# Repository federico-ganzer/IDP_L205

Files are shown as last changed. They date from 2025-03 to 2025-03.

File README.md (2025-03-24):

#  It Doesn’t Perform - L205
This repository is for the Integrated Design Project (IDP) belonging to Team 205 done in Lent 2024-5. 

## Documentation:
- **Software:** ['docs.md'](docs.md)
- **Electrical:** ['IDP___Electrical_Documentation.pdf'](IDP___Electrical_Documentation.pdf) 
- **Mechanical:** [Mechanical Documentation.pdf](https://github.com/federico-ganzer/IDP_L205/blob/main/Mechanical%20Documentation.pdf)

## Our Team:
- Somanshu - Software
- Josh - Electrical/Software
- Alex - Electrical/Mechanical
- Hayyan - Mechanical
- Tom - Mechanical
- Djaafar - Mechanical
- Federico - Software

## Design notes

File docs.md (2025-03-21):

# Team L205 IDP Software Documentation

  


## Table of Contents

1. [Structure and Algorithms](#Structureandapplication)
2. [Modules](#modules)

## Structure and Algorithms
The general approach of the software structure was to create an AGV class (`Robot()`) that could be used to access motor control, sensor readings, and storing of current state variables associated to what the robot's current task is. The AGV class would respond to changes in its current route and move from node to node accordingly. The `current_node` state variable is updated to the next node in the current route whenever a junction is detected. At each detected junction a decision function is called to determine whether the robot should turn, and the `current_direction` variable is adjusted accordingly.
<div align="center">
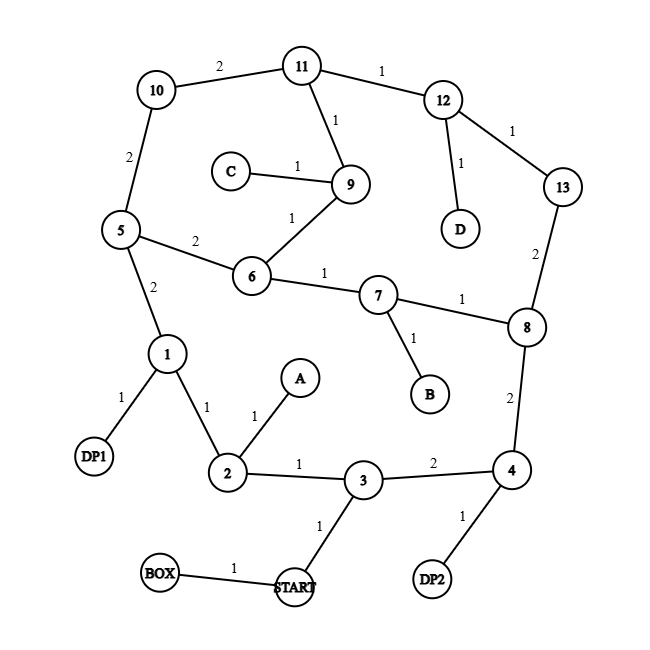
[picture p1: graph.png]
Graph
  
  <p><em>Figure 1: Graph of town with `node_id` and edge values used by `pathfinder.py`</em></p>
</div>

For our use, the `Robot()` pins are set as follows (these can be changed in the pins dict passed to `Robot()` when initializing):
```
pins = {'outer_sensorL_pin' : 18, 'outer_sensorR_pin' : 19,
        'line_sensorR_pin' : 20, 'line_sensorL_pin' : 21,
        'motorR_pwm_pin' : 4, 'motorR_dir_pin' : 5, # Motor Pins are Hard Coded in Robot()
        'motorL_pwm_pin' : 6, 'motorL_dir_pin' : 7, # Motor Pins are Hard Coded in Robot()
        'servo_pin1' : 13, 'servo_pin2' : 15,
        'led_pin' : 22, 'button_pin': 12 }
```
Each number represents the corresponding GPIO pin on the picobot.

The main loop (in `main.py`) starts by initialising the robot with the current target of `A`. Once the robot navigates to its target, it enters the pickup routine and initializes a new route based on the colour of the package it picked up. The route is then navigated, the block is dropped and a new route is initialized to the closest non-visited customer. The process is repeated until all customers have been visited. The robot then returns to the start box.

```mermaid
flowchart TD
    Start([Start]) --> Initialize[Initialize Robot with pins and targets]
    Initialize --> SetServo[Set servo to zero]
    SetServo --> |Move Forward| MoveForward[Move forward at speed 100 along current_route]

    MoveForward --> |Check Current Node| CheckNode{Is current node in customers?}
    CheckNode --> |Yes| Pickup[Perform pickup operation]
    CheckNode --> |No| CheckDepot{Is current node in depots?}

    Pickup --> |Continue| MoveForward

    CheckDepot --> |Yes| Drop[Perform drop operation]
    CheckDepot --> |No| MoveForward

    Drop --> |Find Closest Customer| FindClosest[Find closest unvisited customer]
    FindClosest --> |Update Target and Route| UpdateTarget[Set current_target and current_route]
    UpdateTarget --> |Continue| MoveForward

    Drop --> |Check if All Customers Visited| CheckAllVisited{Are all customers visited?}
    CheckAllVisited --> |Yes| ReturnToStart[Set target to START and plan route]
    CheckAllVisited --> |NO| FindClosest
    ReturnToStart --> |Continue| MoveForward

    MoveForward --> |Check if at START| CheckStart{Is current node START and target START?}
    CheckStart --> |Yes| Stop[Stop motors and end program]
    CheckStart --> |No| MoveForward

    Stop --> End([End])
```
<div align="center">
<p><em>Figure 2: Diagram of main loop</em></p>
</div>

## Modules
- [robot.py](#robot.py)
- [pathfinder.py](#pathfinder.py)
- [Sensors](#sensors)
- [motors.py](#motors.py)

### `robot.py`

**Description:** Contains `Robot(i2c_bus, pins[dict], start, target1)` class. `Robot()` contains methods for AGV control for manouvring and collecting/depositing loads. Class is initialised with i2c pins and pin numbers associated with the servos, motors and sensors and can be easily modified as a modular system (eg. if sensor or servo additions are made). `start` and `target1` (in `node_id` form) are necessary to set the first route the `Robot()` should follow.

**Methods:**
-  `forward()`: Drives robot motors at desired speed with line following and junction decision logic. Uses PID control for straight line following from [`follow_line()`](#follow_line).

-  `turn()`: Following a call to [`junction_decision()`](#junction_decision), the robot performs a 90 degree turn in the direction set by `junction_decision()`, provided that junction type also satisfies the turn. The current state variables are then updated. This checks that the middle sensor (on the side opposite to that of the direction of tha turn) is on the line and then exits the function, such that the PID control in `forward()` is reinitiated. Boolean `with_prep = True` determines if a turning prep-time should be added. During this prep-time the robot continues forward for a set time interval before turning. `with_prep` should be turned false if turning from a reverse position.

-  `junction_decision()`: Using a 2D vector product between the current and next direction, the function returns a value that when positive indicates a left turn, when negative, a right turn, and when zero straight. If the `Robot()` is at the end of the `current_route`, the robot stops.

-  `detect_junction()`: Uses the two outer line sensors to detect junctions. If a junction is detected [`junction_decision()`](#junction_decision) is called and the position of `current_node`(graphical representation of position) is updated in [`forward()`](#forward).

-  `follow_line()`: Implements PID control with two line sensor inputs straddling the line to follow the line. PID weights can be adjusted in `self.kp`, `self.ki`, and `self.kd`.

-  `spin()`: Performs a spin by 180 degrees. This will check that the configuration of the robot has now been realligned also (to an approximate degree) before the `follow_line()` takes over again.

-  `pickup()`: Routine actuates the servo to pick up the block. The colour of the block is identified and the according depot is assigned as the `self.current_target`, creating a new route for `Robot()` to follow in forward. The `Robot()` will turn out of the customer zone accordingly.

-  `drop()`: Actuates the servo to drop the block. Then the next closest customer is determined for `Robot()`. The `Robot()` turns out of the depot, facing away from the wall to avoid collision, and then exits the routine. 

### `pathfinder.py`

**Description:** Makes use of adjacency table of graph and Dijkstra's algorithm to find the minimal distance path from a given `start` node to `end` node. Includes a map from each node to their coordinate in physical space, which is used to determine which direction turns need to be made in.

**Functions:**
- `dijkstra(adj_list, start, end)`: Applies dijkstra's algorithm between `start` and `end` nodes (in `node_id` form) when prodived with `adj_list` of the underlying graph (map) and returns a tuple containing the list of the coordinates of nodes in a route (not including `start`) and the total length of the route.

- `convert_coord_to_node(coord)`: Uses the `coord_to_node` dictionary to convert phyical coordinates of nodes to their respective `node_id`.

### `motors.py`
**Description:** Includes two class definitions that are used primarily in the `robot.py`, that controls the motor movements as well as servo movements. 

#### `Motor(dir_pin, pwm_pin)`
Takes parameters of the pins used, and has the following methods:
- `self.forward(speed)`
- `self.reverse(speed)`
- `self.stop()`

#### `Servo(pwn_pin)`
Takes parameters of the pin (singular) used. It has the following methods:
- `set_angle(angle)`
- `zero()`

### Sensors
**File:** `tcs34725.py`
**Description:**  Includes the class TCS34725, which contains methods for initialising the colour sensor as well as reading the colour temperature, which is used in [`pickup()`](#pickup) to identify the colour of the block that has been picked up. 

**File:** `vl53l0x.py`
**Description:** Includes the class for the ToF sensor, which is not used but could be implemented in the `Robot()` class.

## License

```
MIT License

Copyright (c) 2024 

Permission is hereby granted, free of charge, to any person obtaining a copy
of this software and associated documentation files (the "Software"), to deal
in the Software without restriction, including without limitation the rights
to use, copy, modify, merge, publish, distribute, sublicense, and/or sell
copies of the Software, and to permit persons to whom the Software is
furnished to do so, subject to the following conditions:

The above copyright notice and this permission notice shall be included in all
copies or substantial portions of the Software.

THE SOFTWARE IS PROVIDED "AS IS", WITHOUT WARRANTY OF ANY KIND, EXPRESS OR
IMPLIED, INCLUDING BUT NOT LIMITED TO THE WARRANTIES OF MERCHANTABILITY,
FITNESS FOR A PARTICULAR PURPOSE AND NONINFRINGEMENT. IN NO EVENT SHALL THE
AUTHORS OR COPYRIGHT HOLDERS BE LIABLE FOR ANY CLAIM, DAMAGES OR OTHER
LIABILITY, WHETHER IN AN ACTION OF CONTRACT, TORT OR OTHERWISE, ARISING FROM,
OUT OF OR IN CONNECTION WITH THE SOFTWARE OR THE USE OR OTHER DEALINGS IN THE
SOFTWARE.
```

---

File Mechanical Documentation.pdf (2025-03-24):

Mechanical Documentation

Assembly Drawing
Laser Cut MDF Part Drawings Sheet Metal Drawings
DFX Files Used for Laser Cutting

Material Choice

The two main materials in manufacturing were MDF and 1.4mm Aluminum plate. MDF was chosen over Plywood due to it being slightly stronger and less flexible, without really affecting the weight. Aluminum was chosen over Steel, as it was thicker for a similar weight and hence resulted in less bending and warping. We chose not to do any 3D printing as this is time consuming and didn't allow for rapid prototyping and modification.

Assembly

We preferred to use bolts when assembling as this allowed for easy deconstruction and modification. Wood glue was used to fit together the finger joint boxes for the Picobot and the Battery. We also sometimes had to make use of washers and bolts to offset pieces to the required position. Holes for bolts are marked on the sheet metal pieces in the drawing, although there are no holes marked on the drawings for wooden pieces as we found it easy to simply mark these holes with a pencil using the holes from the other pieces that were to be fitted, this allowed for the best positioning and alignment.

E

E

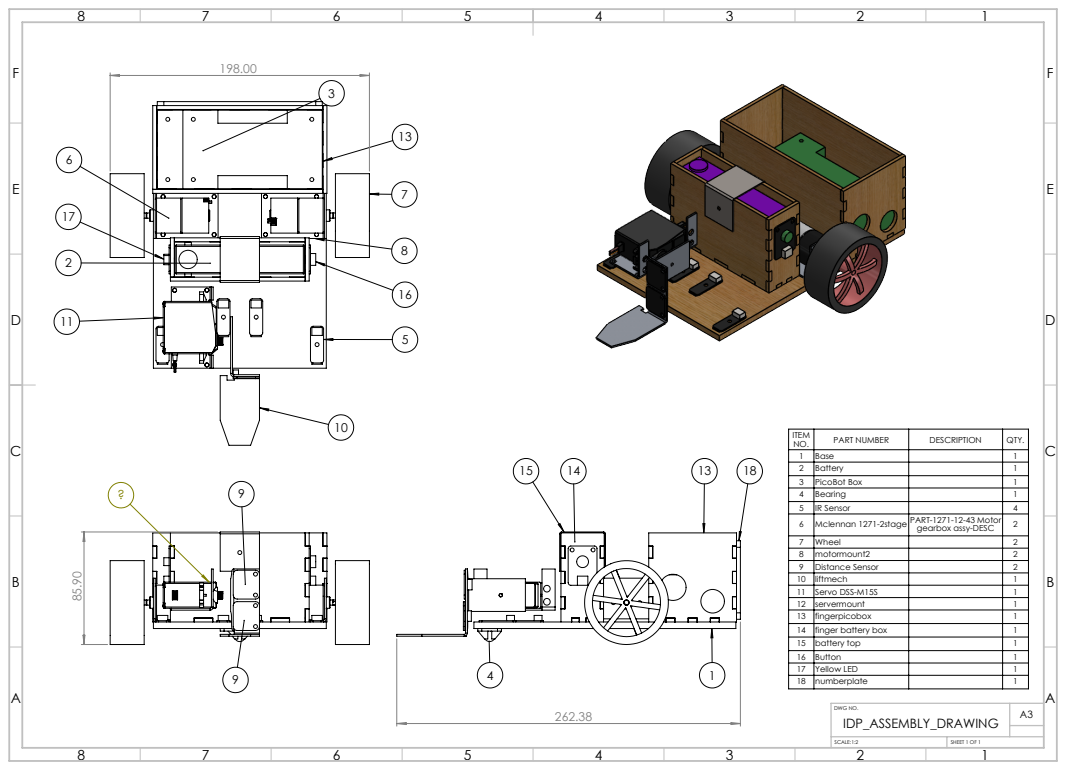
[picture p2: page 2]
ITEM; PART NUMBER; DESCRIPTION; QTY. 1; Base; Battery; PicoBot Box; Bearing; IR Sensor; Mclennan 1271-2stage PART-1271-12-43 Motor; SHEET 1 OF 1; IDP_ASSEMBLY_DRAWING; SCALE:1:2; DWG NO.

gearbox assy-DESC | 2

7 | Wheel | | 2
8 | motormount2 | | 2
9 | Distance Sensor | | 2
10 | liftmech | | 1
11 | Servo DSS-M15S | | 1
12 | servermount | | 1
13 | fingerpicobox | | 1
14 | finger battery box | | 1
15 | battery top | | 1
16 | Button | | 1
17 | Yellow LED | | 1
18 | numberplate | | 1

G | G
H | H

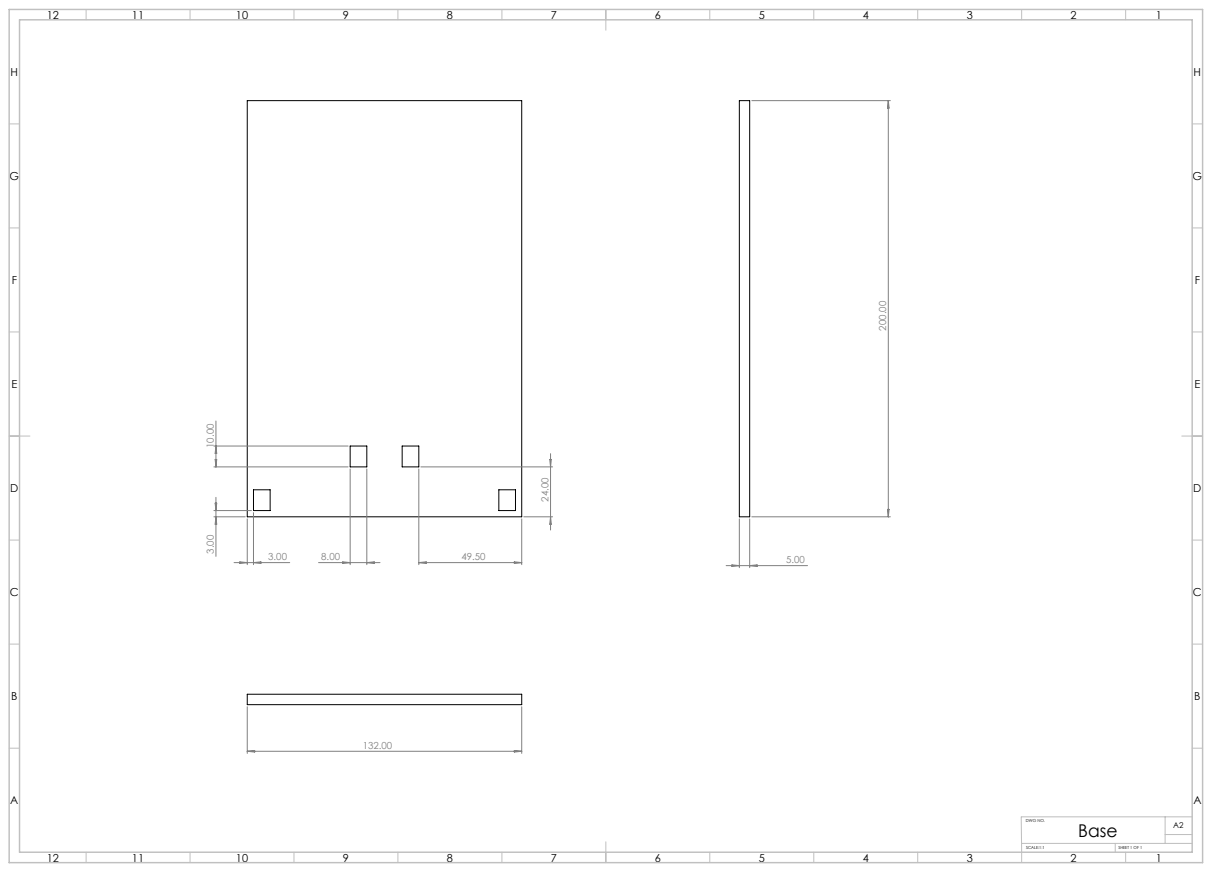
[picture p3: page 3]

Base

SCALE:1:1 | SHEET 1 OF 1

G | G
H | H

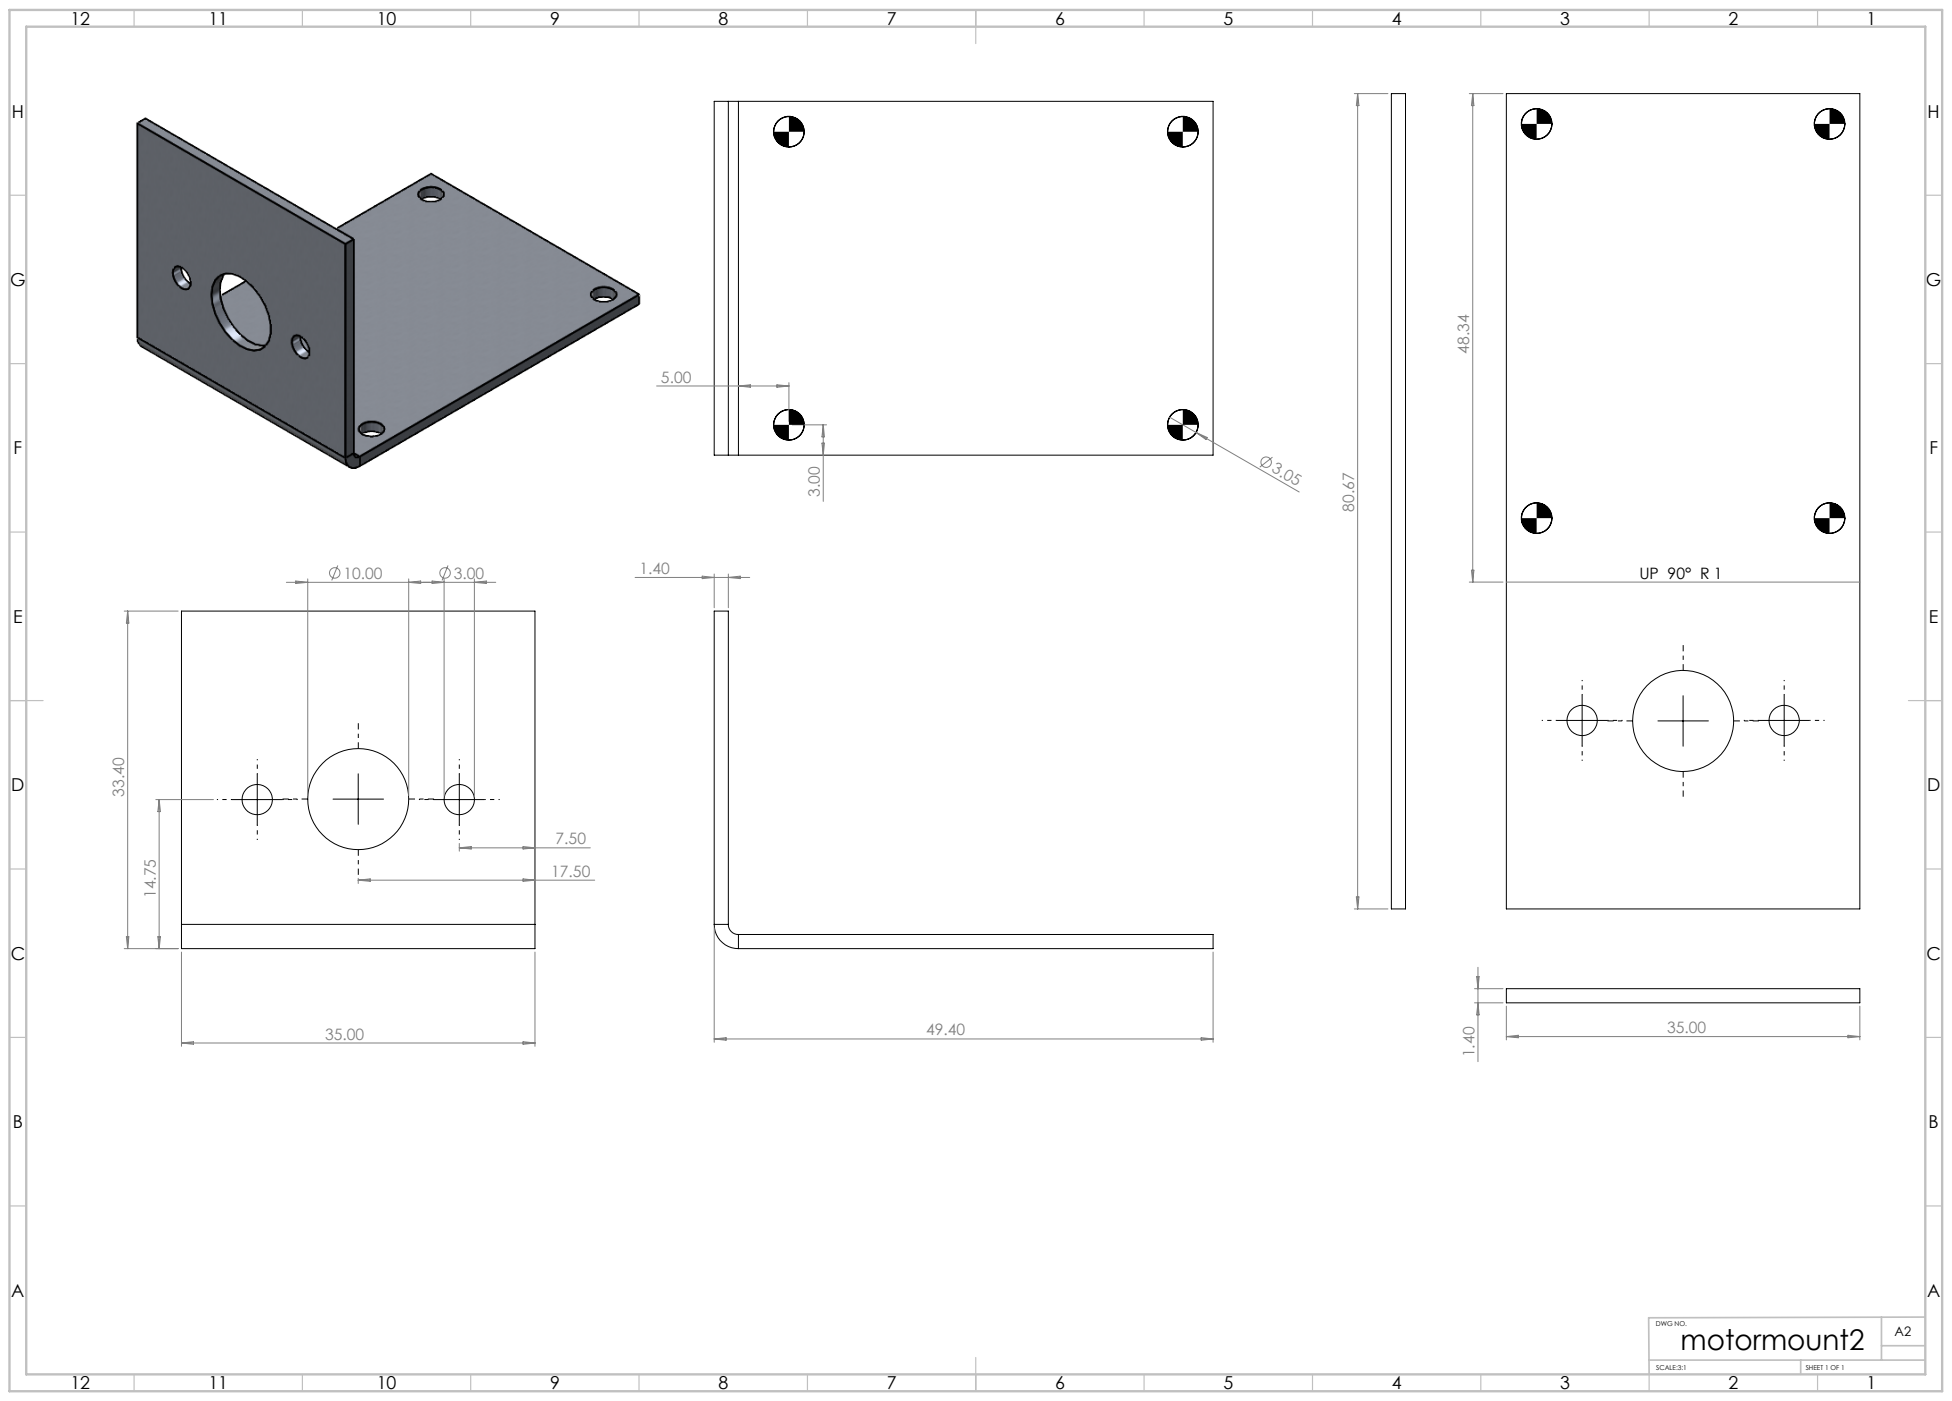
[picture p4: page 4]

motormount2

SCALE:3:1 | SHEET 1 OF 1

G

G

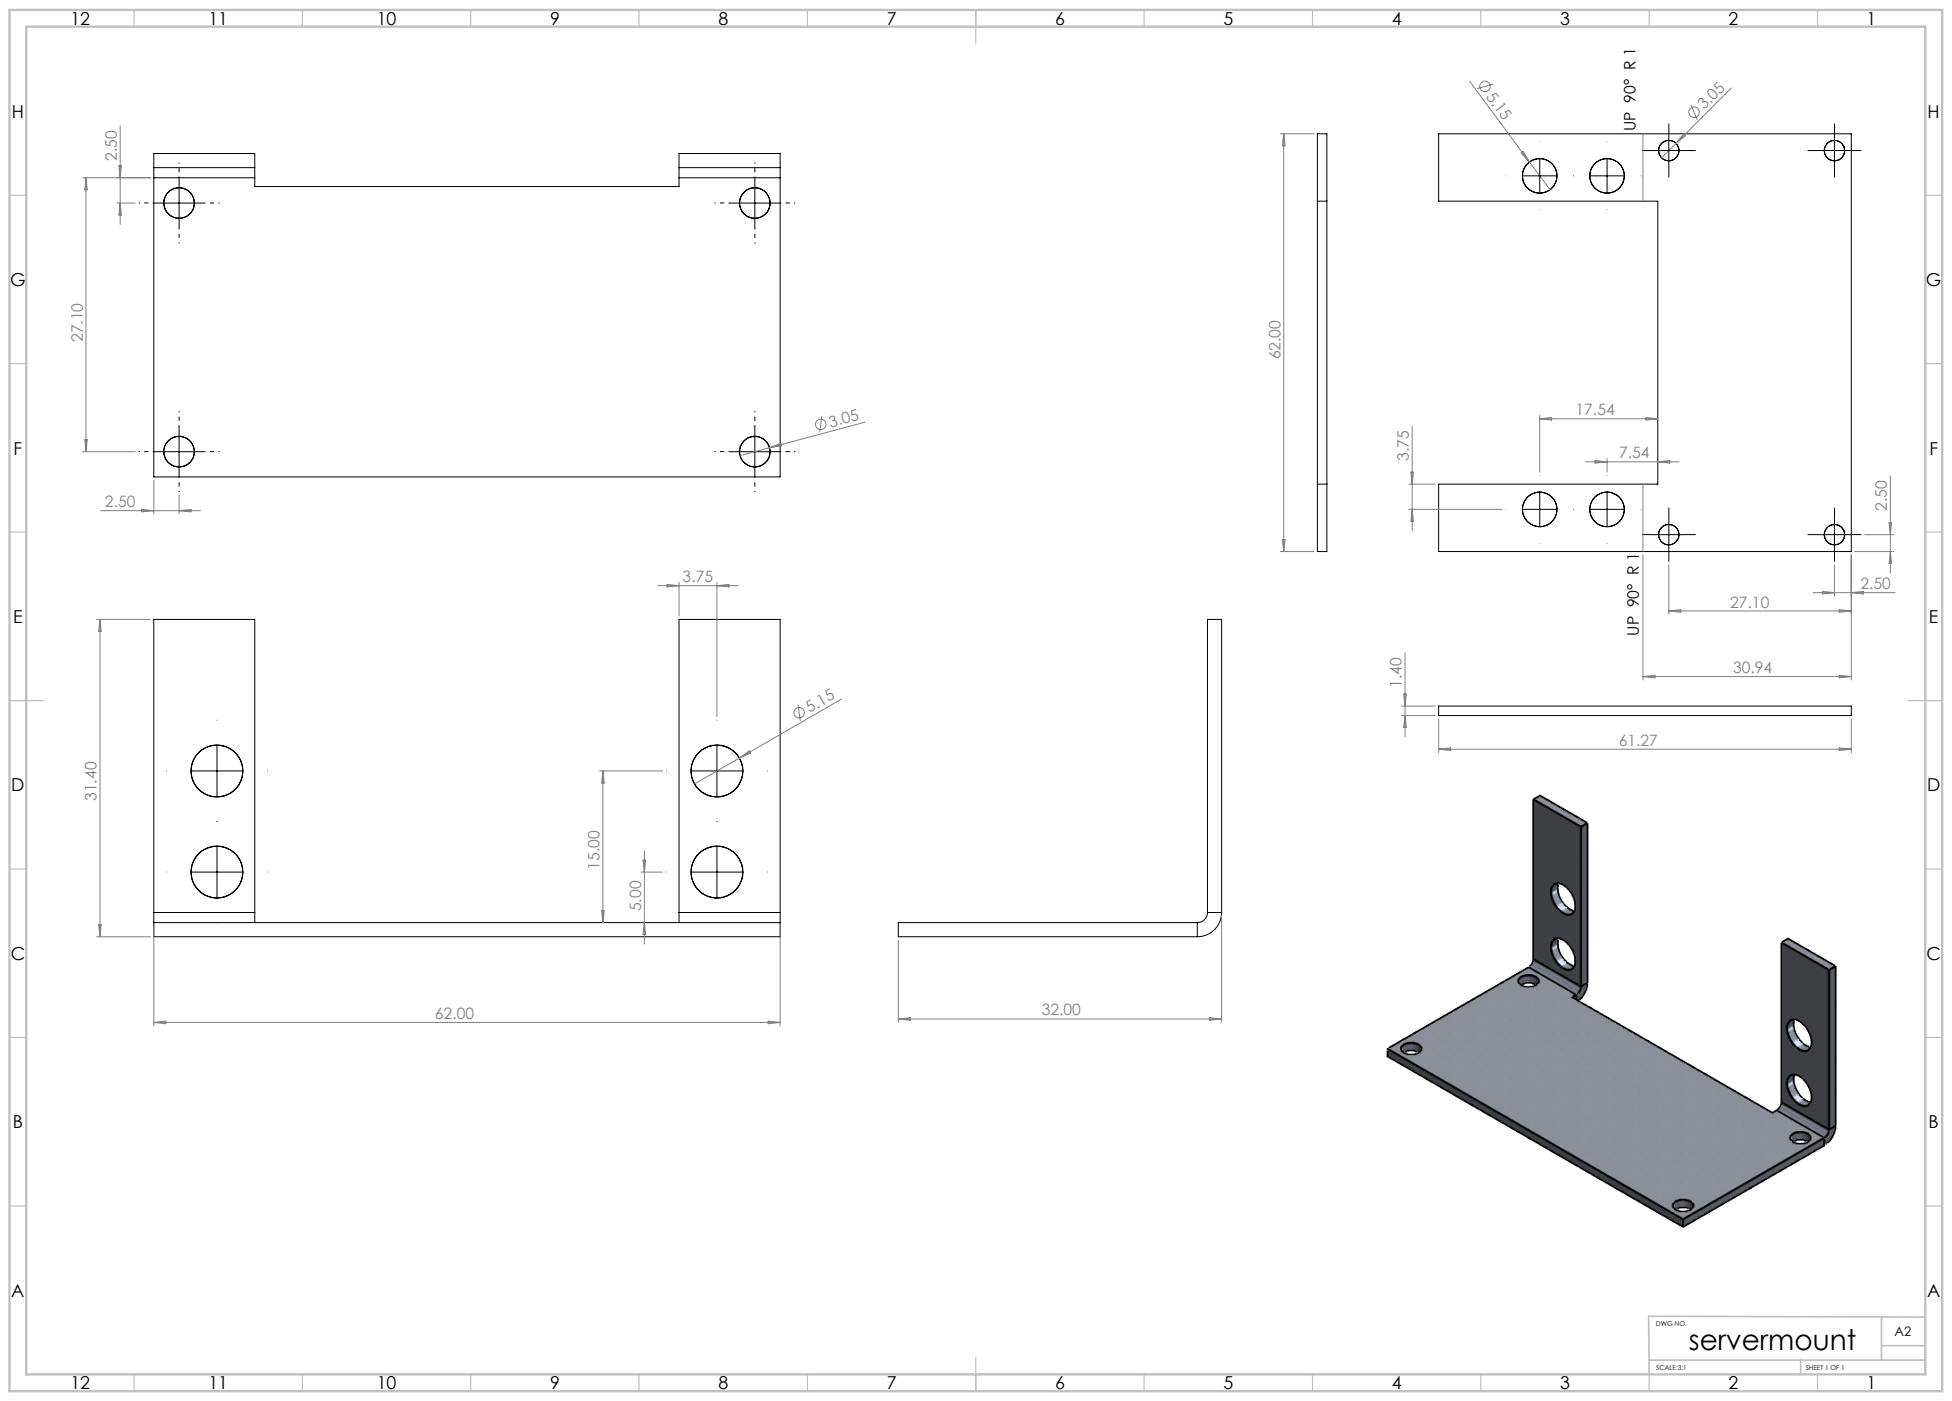
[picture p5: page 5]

servermount

SCALE:3:1 | SHEET 1 OF 1

G

G

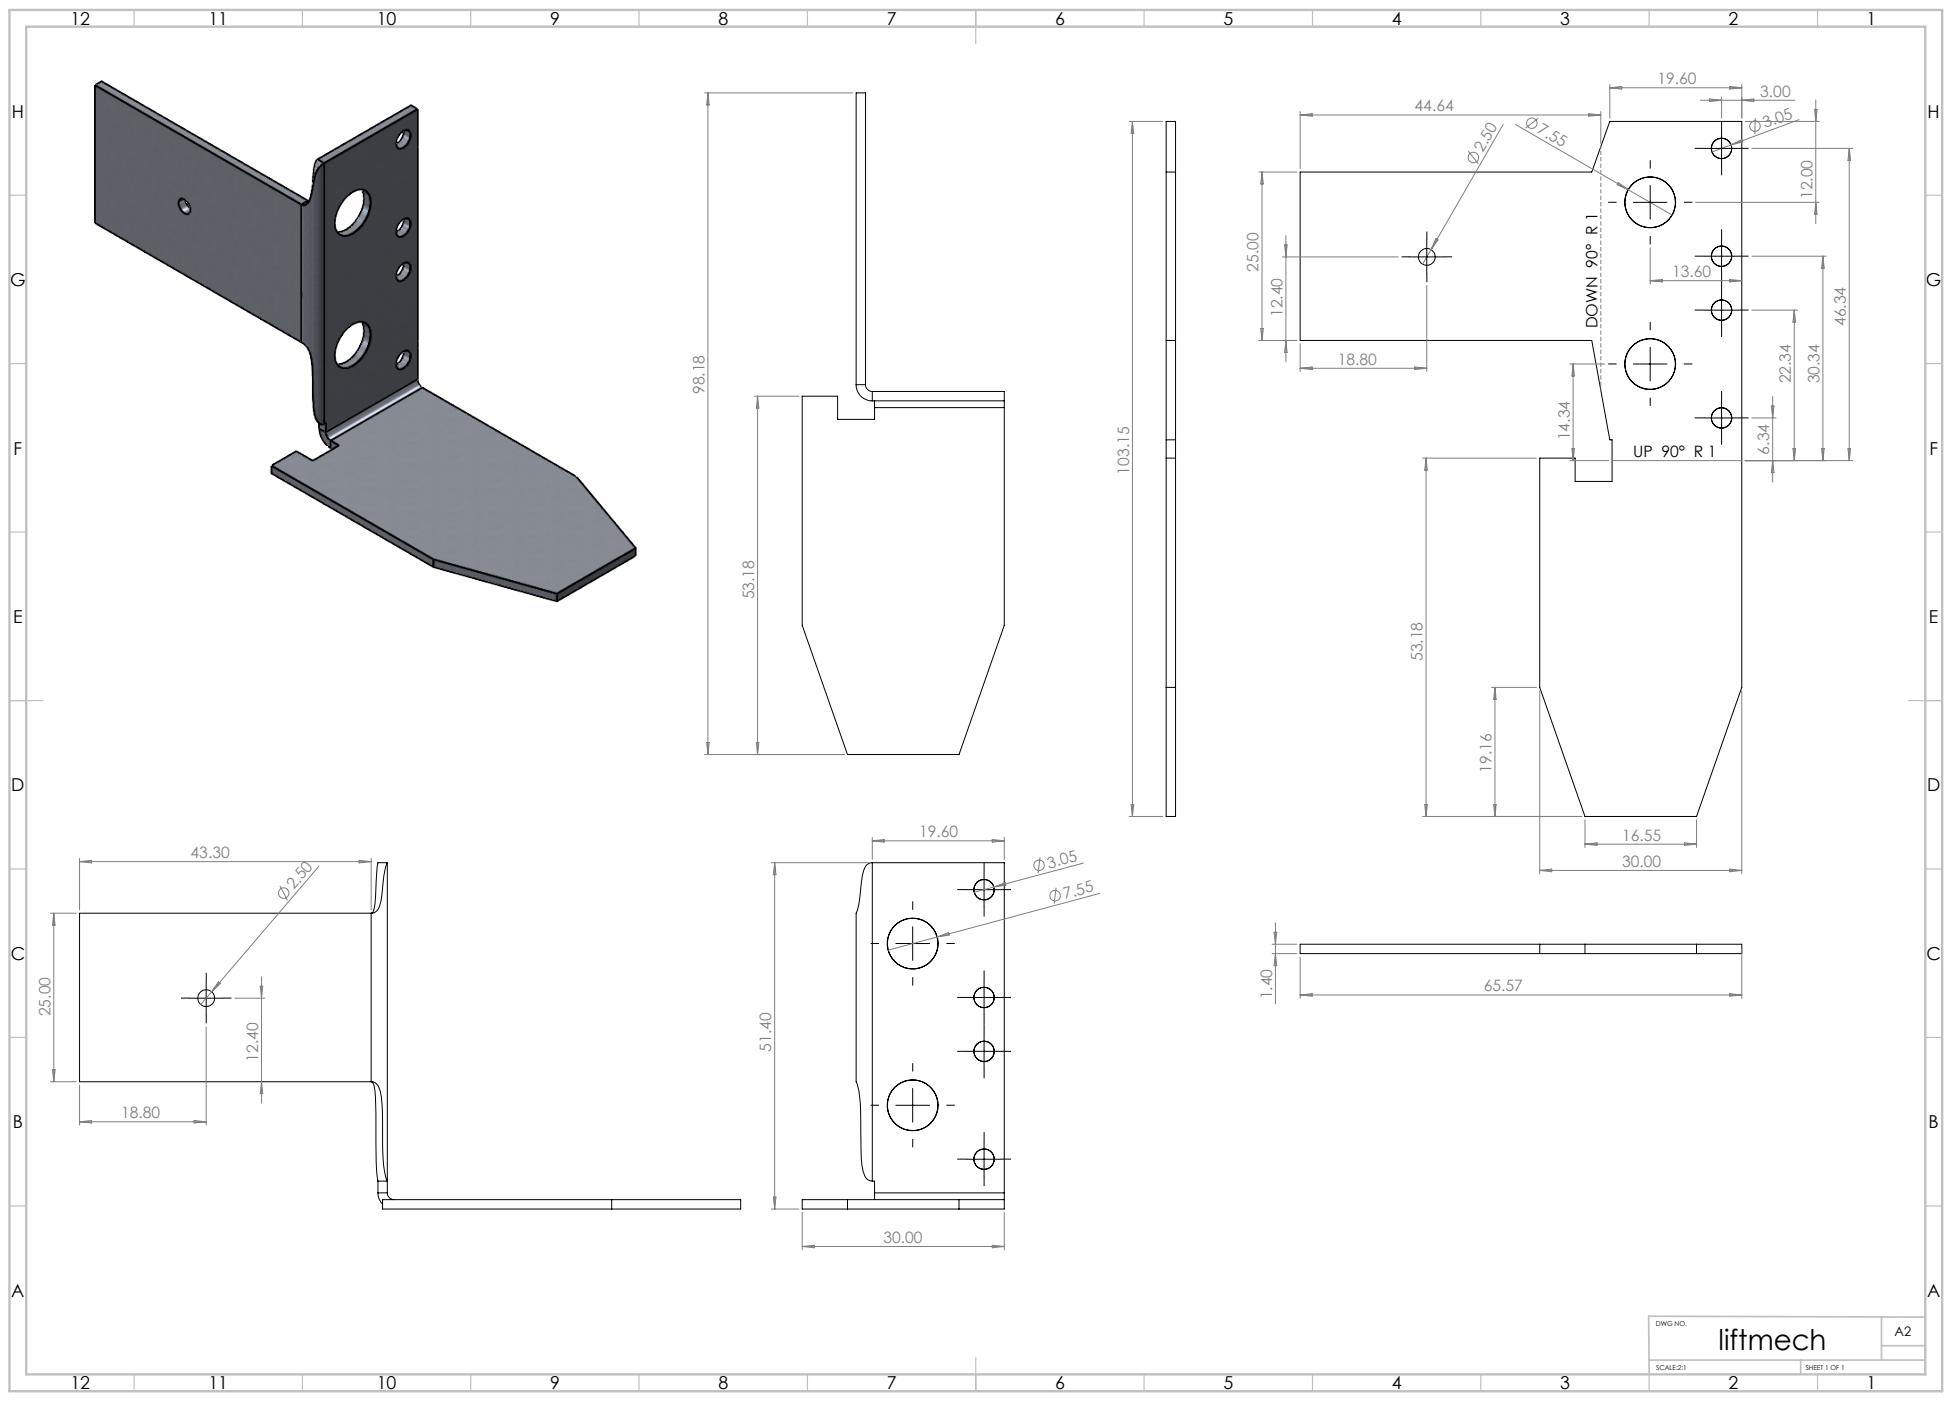
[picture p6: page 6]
DOWN 90° R 1

liftmech

SCALE:2:1 | SHEET 1 OF 1

G | G
H | H

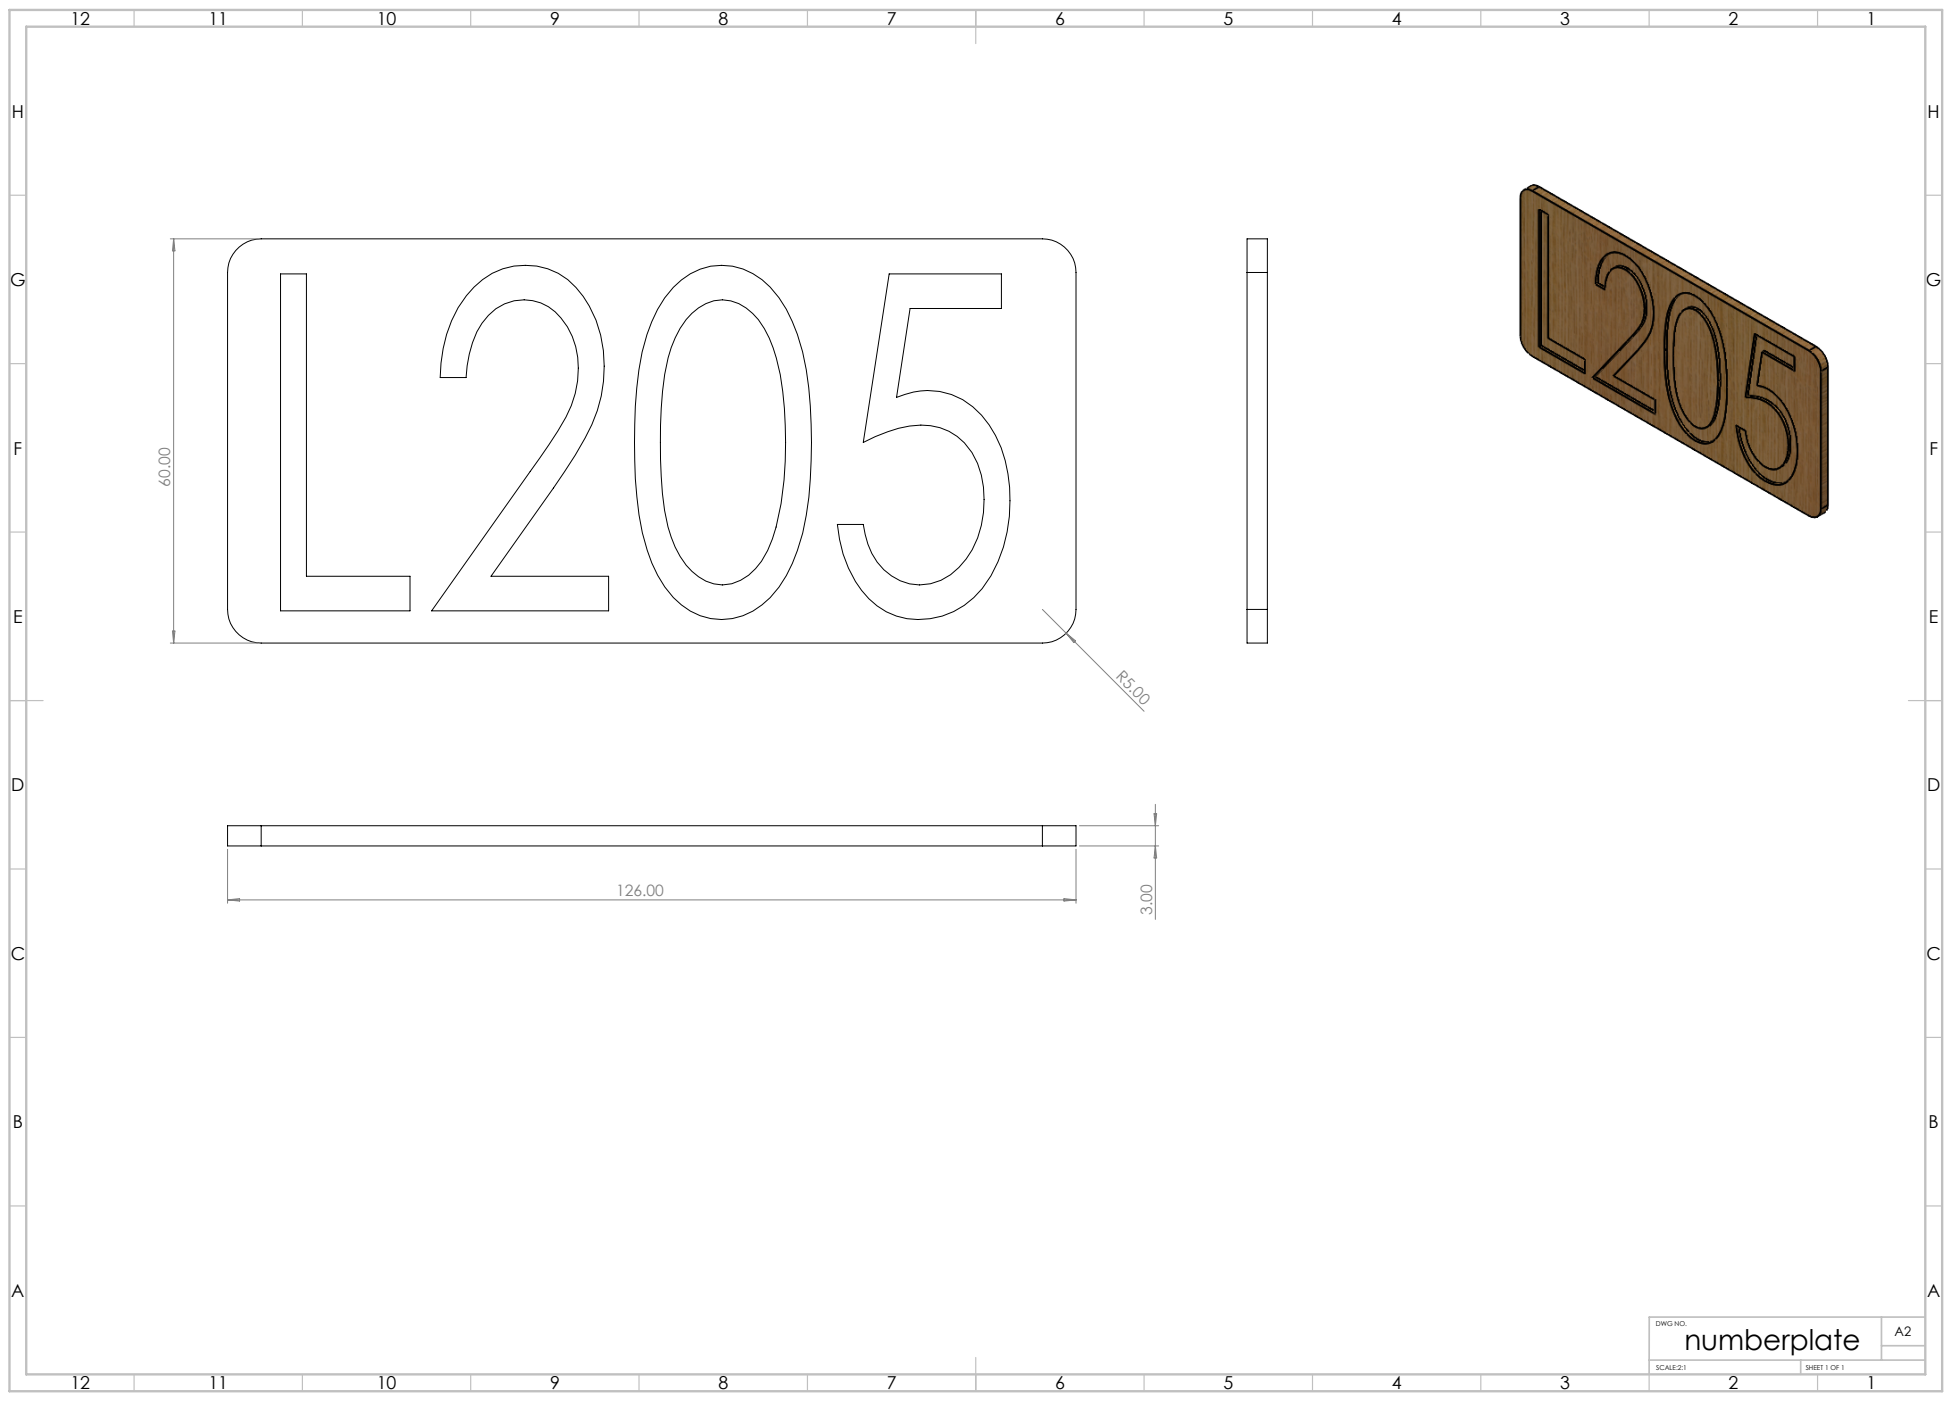
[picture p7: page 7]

numberplate

SCALE:2:1 | SHEET 1 OF 1

G | G
H | H

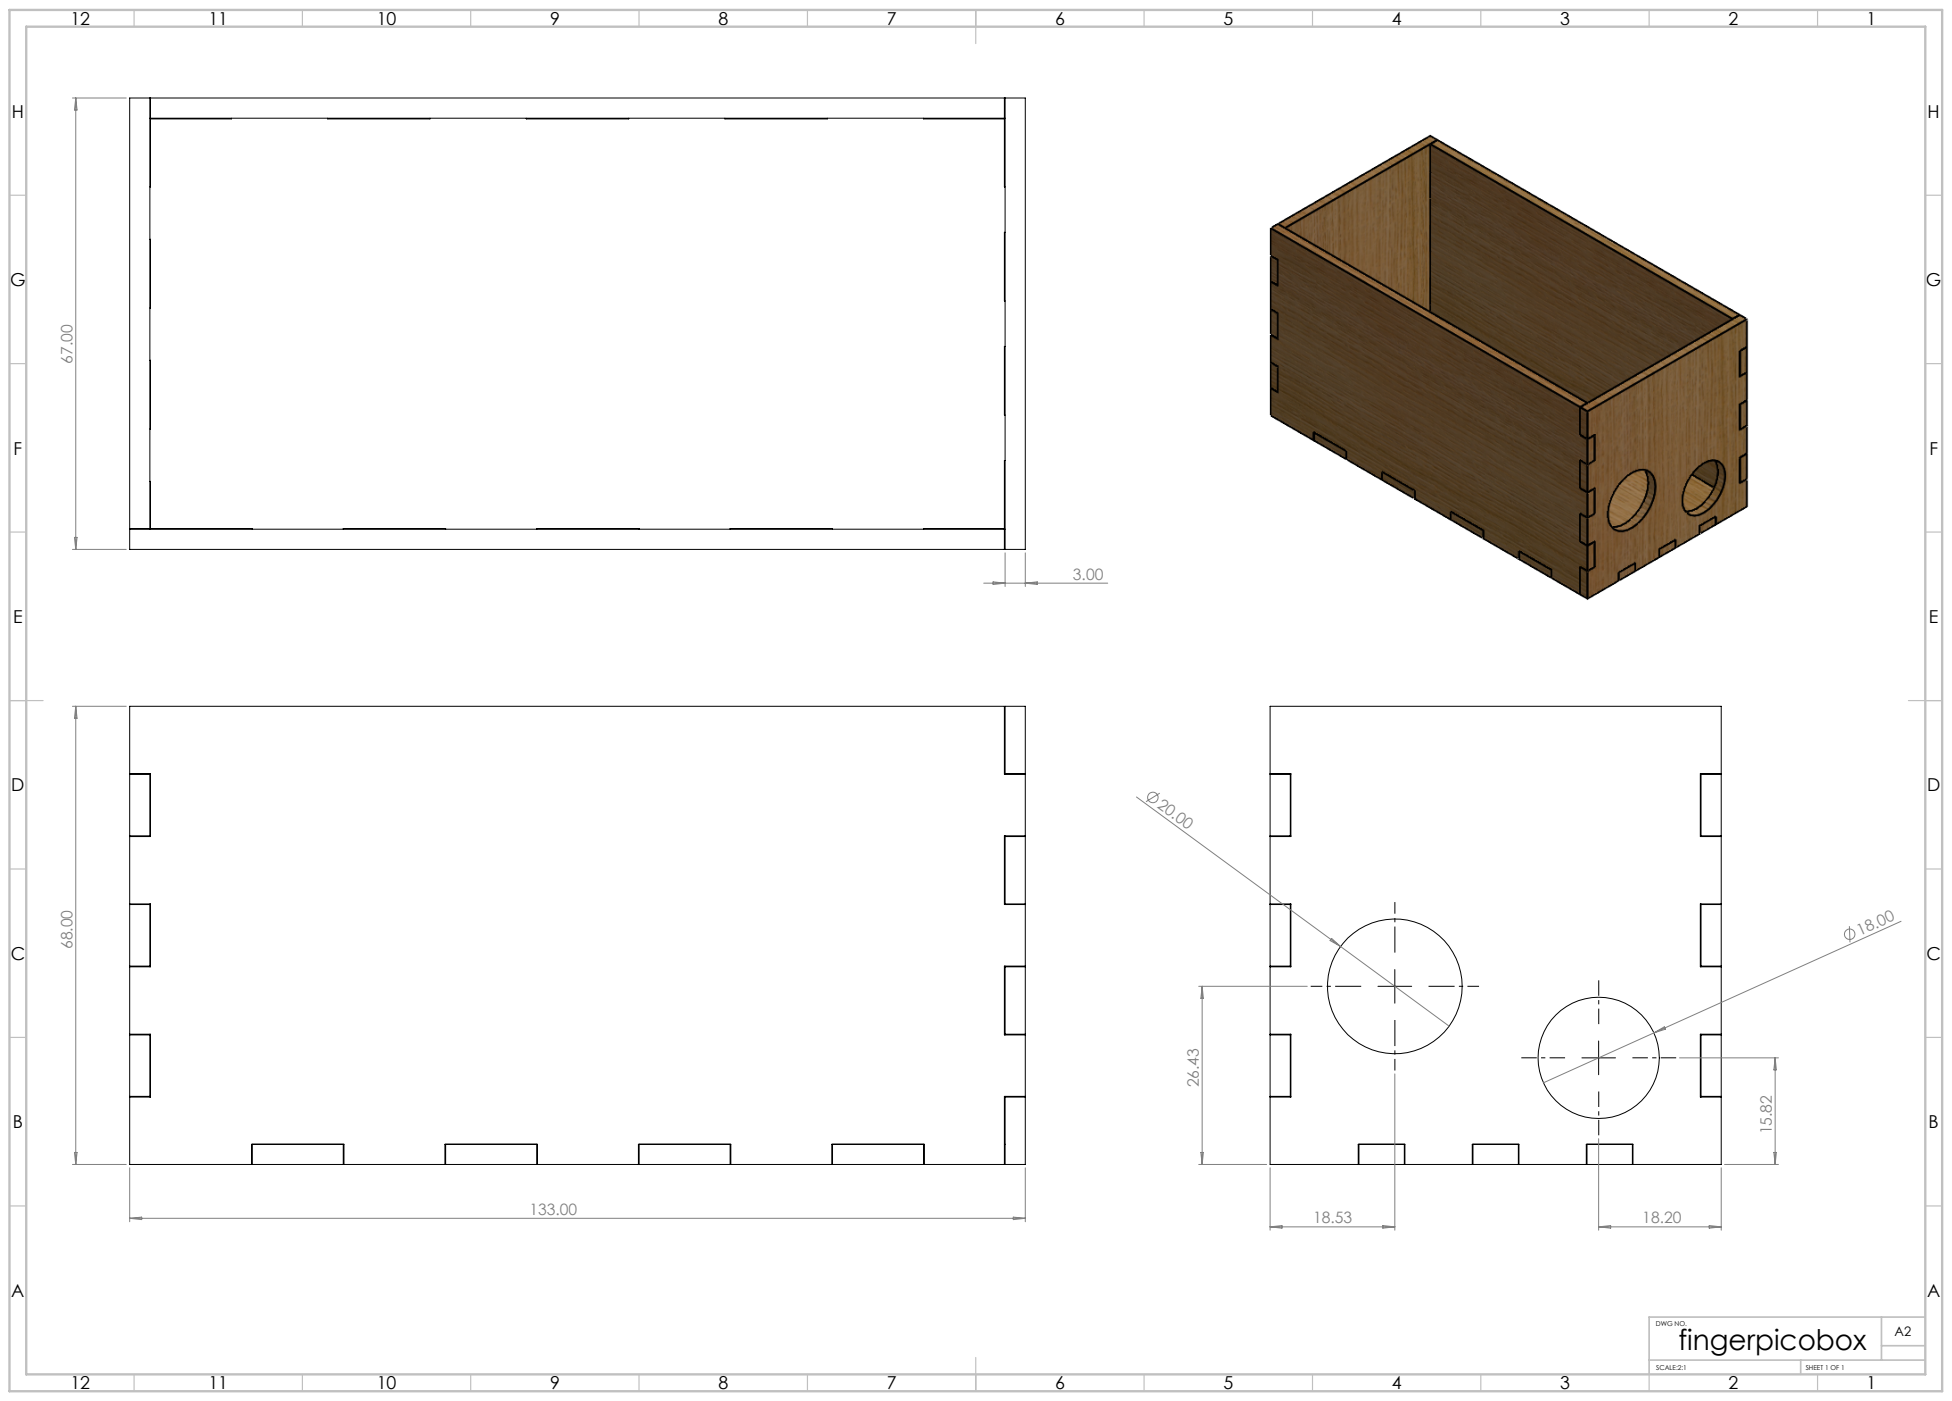
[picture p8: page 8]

fingerpicobox

SCALE:2:1 | SHEET 1 OF 1

G | G
H | H

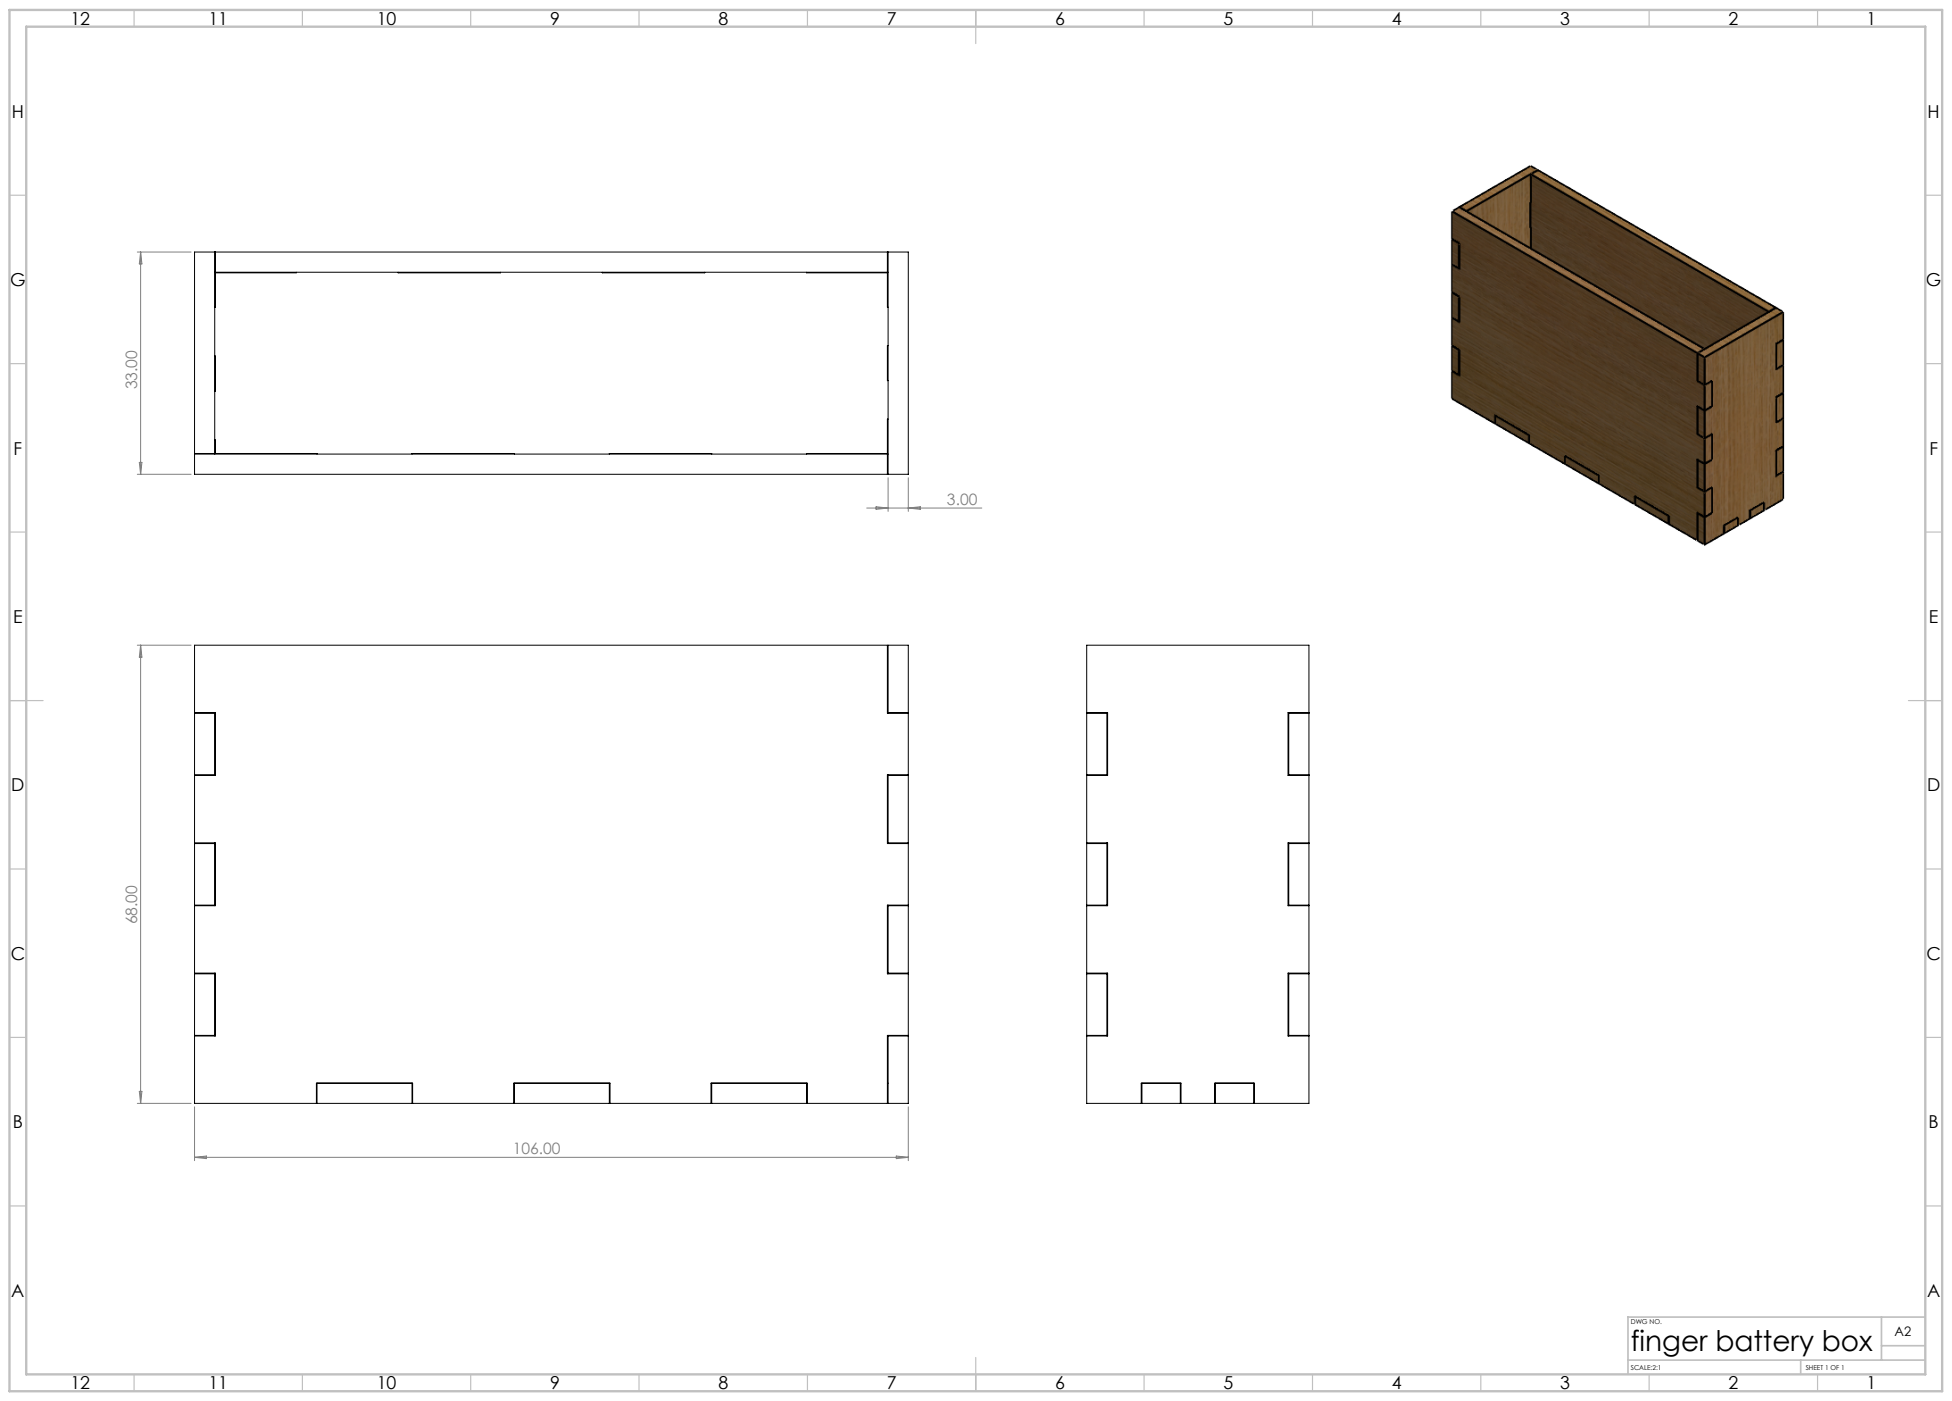
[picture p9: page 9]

finger battery box

SCALE:2:1 | SHEET 1 OF 1

G

G

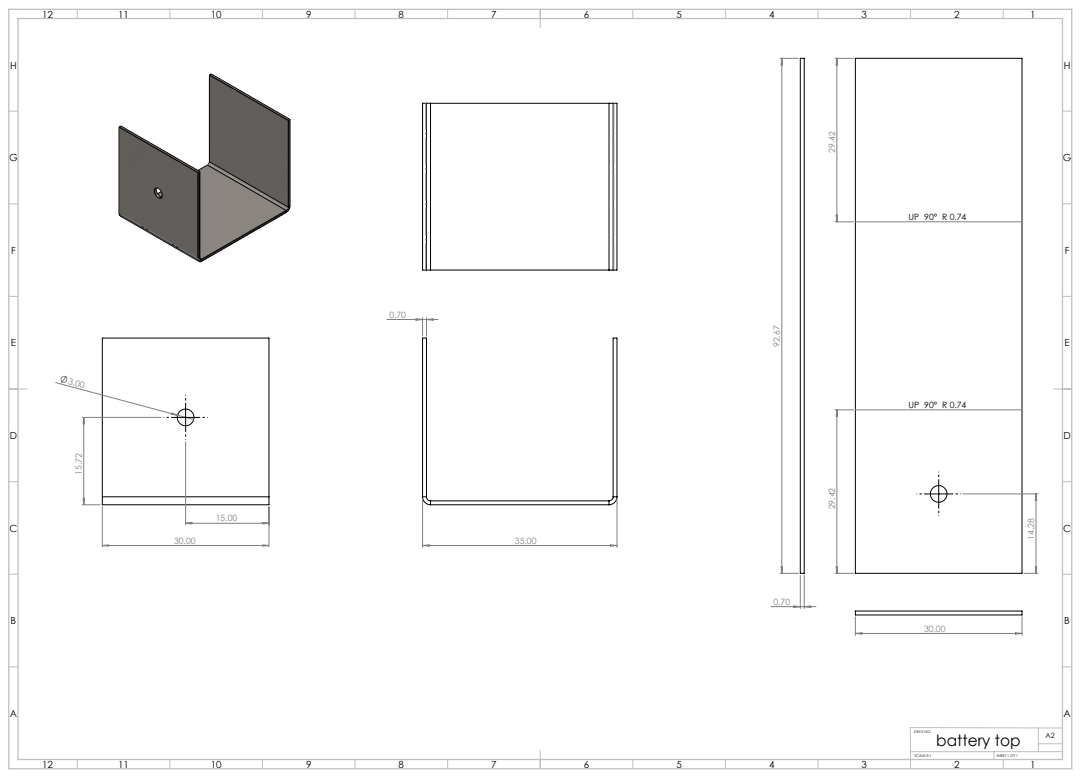
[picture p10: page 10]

battery top

SCALE:3:1 | SHEET 1 OF 1

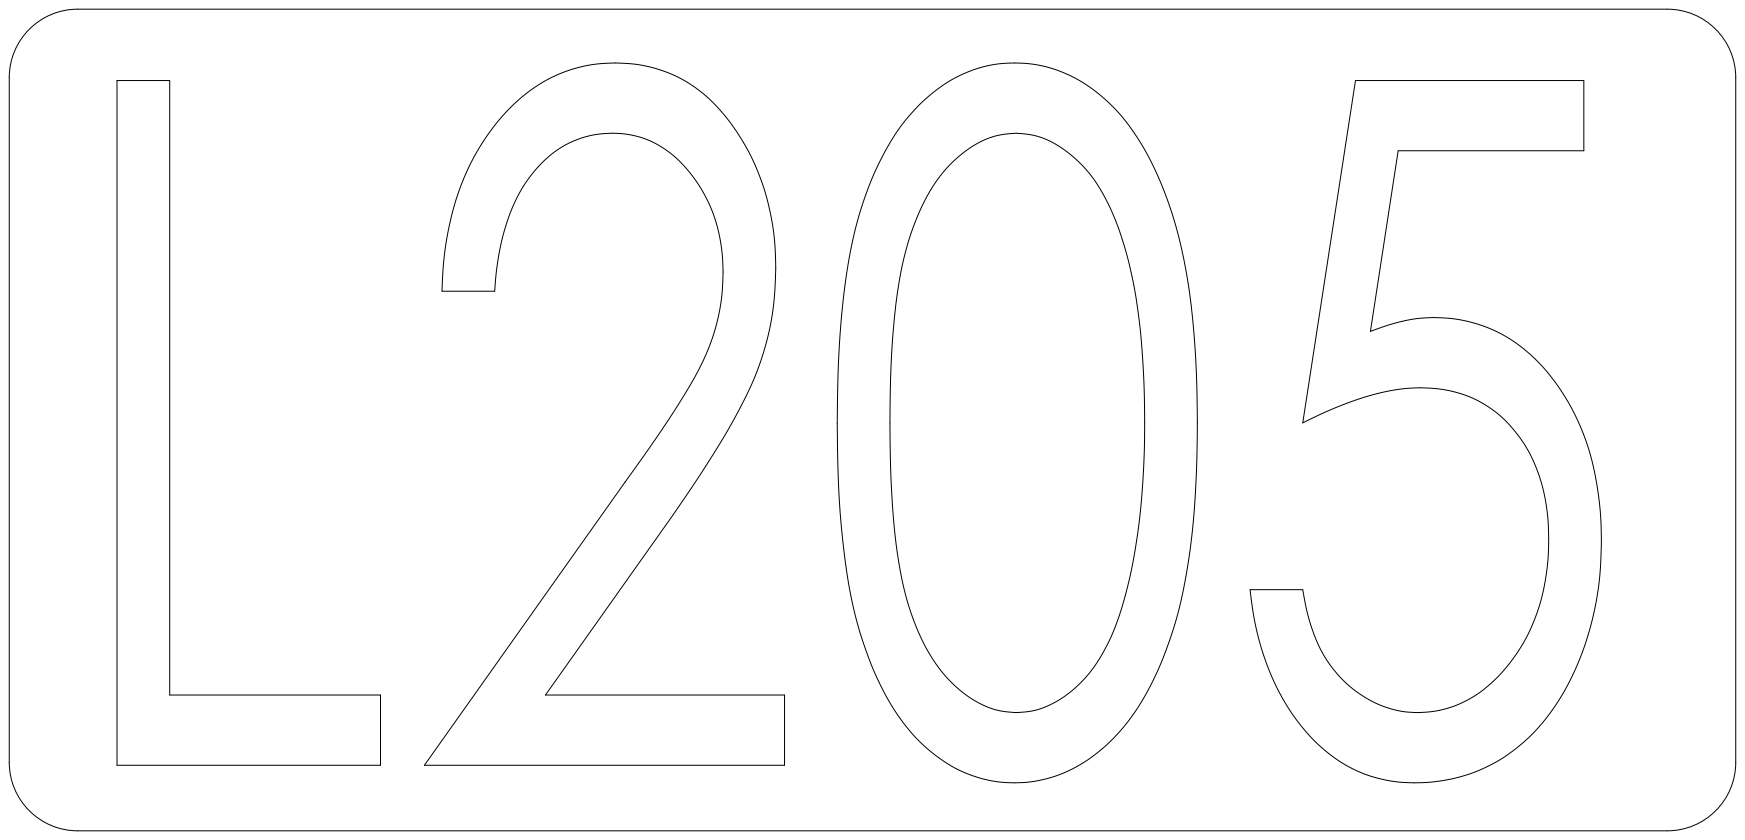
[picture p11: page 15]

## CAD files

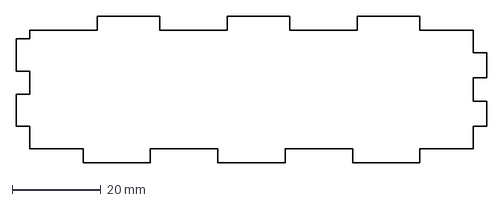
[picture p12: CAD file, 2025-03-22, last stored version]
Mechanical Documentation/DXF Files/Battery Box 5.DXF
106.0 x 33.0 mm

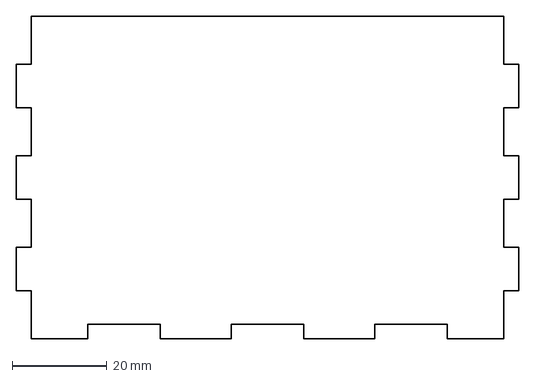
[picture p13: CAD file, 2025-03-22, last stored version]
Mechanical Documentation/DXF Files/Battery Box 2.DXF
106.0 x 68.0 mm

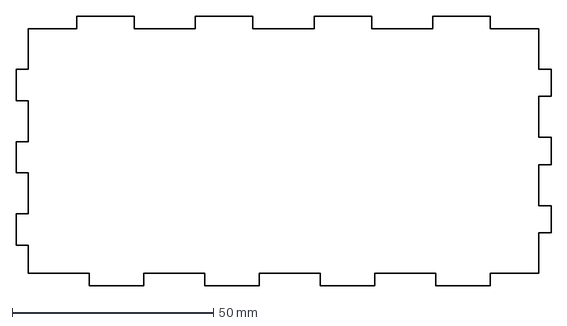
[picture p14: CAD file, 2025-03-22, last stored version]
Mechanical Documentation/DXF Files/Picobot Box 1.DXF
133.0 x 67.0 mm

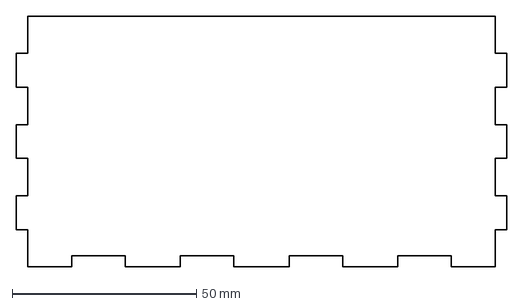
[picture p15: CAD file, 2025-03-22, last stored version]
Mechanical Documentation/DXF Files/Picobot Box 5.DXF
133.0 x 68.0 mm

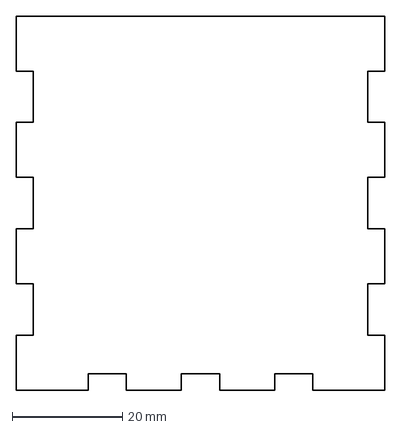
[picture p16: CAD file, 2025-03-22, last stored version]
Mechanical Documentation/DXF Files/Picobot Box 2.DXF
67.0 x 68.0 mm

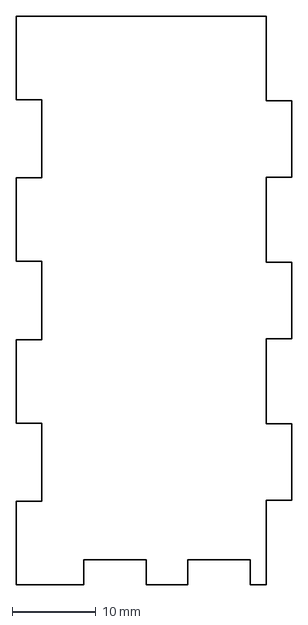
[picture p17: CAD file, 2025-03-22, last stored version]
Mechanical Documentation/DXF Files/Battery Box 4.DXF
33.0 x 68.0 mm

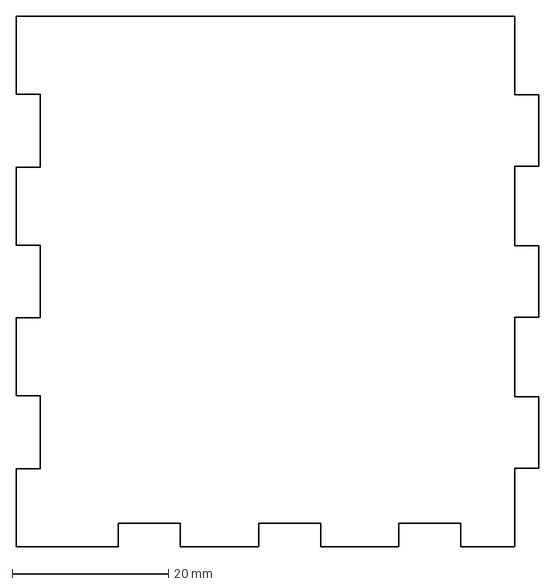
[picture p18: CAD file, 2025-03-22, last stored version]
Mechanical Documentation/DXF Files/Picobot Box 3.DXF
67.0 x 68.0 mm

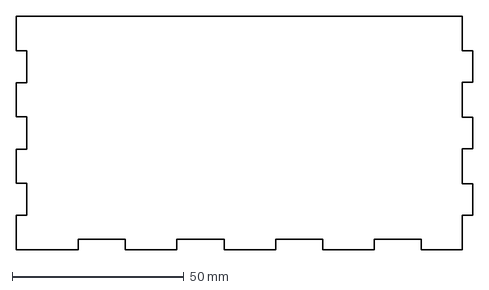
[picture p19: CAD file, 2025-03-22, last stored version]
Mechanical Documentation/DXF Files/Picobot Box 4.DXF
133.0 x 68.0 mm

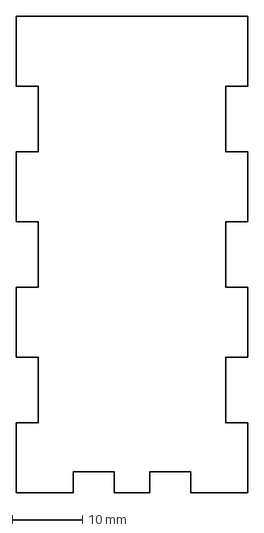
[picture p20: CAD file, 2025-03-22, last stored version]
Mechanical Documentation/DXF Files/Battery Box 3.DXF
33.0 x 68.0 mm

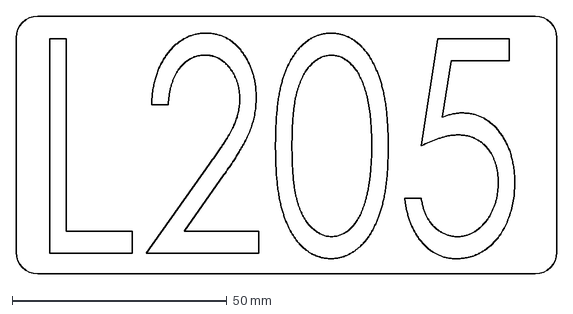
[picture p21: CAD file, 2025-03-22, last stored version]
Mechanical Documentation/DXF Files/Number Plate.DXF
126.0 x 60.0 mm

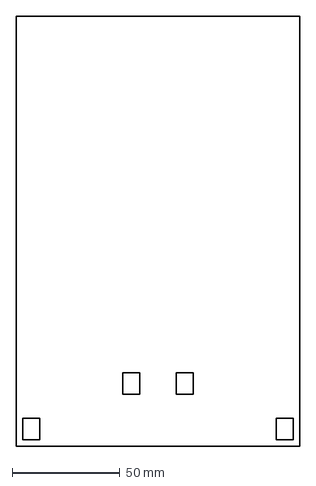
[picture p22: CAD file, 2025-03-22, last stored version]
Mechanical Documentation/DXF Files/Base.DXF
132.0 x 200.0 mm

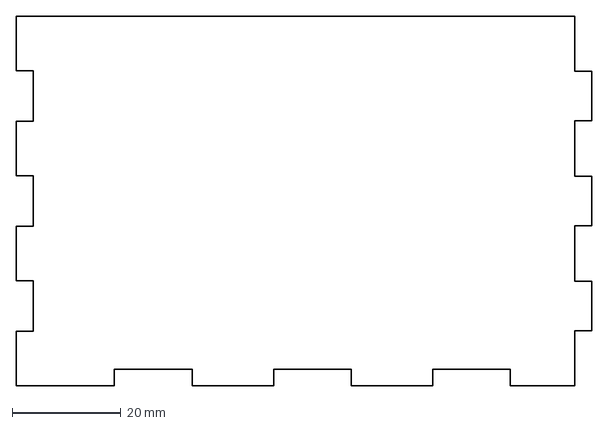
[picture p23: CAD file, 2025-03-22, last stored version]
Mechanical Documentation/DXF Files/Battery Box 1.DXF
106.0 x 68.0 mm

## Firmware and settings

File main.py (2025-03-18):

from robot import Robot
from machine import I2C, Pin
from time import sleep
from pathfinder import dijkstra

i2c_bus_1 = I2C(0, sda= Pin(16), scl= Pin(17), freq= 400000)

pins = {'outer_sensorL_pin' : 18, 'outer_sensorR_pin' : 19,
        'line_sensorR_pin' : 20, 'line_sensorL_pin' : 21,
        'motorR_pwm_pin' : 4, 'motorR_dir_pin' : 5, # Motor Pins are Hard Coded in Robot()
        'motorL_pwm_pin' : 6, 'motorL_dir_pin' : 7, # Motor Pins are Hard Coded in Robot()
        'servo_pin1' : 13, 'servo_pin2' : 15,
        'led_pin' : 22, 'button_pin': 12 }

# Robot class
agv = Robot(i2c_bus_1, pins, start= 'BOX', target1= 'A') # Start at BOX and go to A
 # Test Route from START to A
customers = set(['A', 'B', 'C', 'D'])

def main():
    agv.servo1.zero() # set servo to zero 
    
    while True:
        
        agv.forward(100)

        if agv.current_node in customers:
            agv.pickup() # backout() and turn() included.
            
        if agv.current_node in set(['DP1', 'DP2']):
            agv.drop() # spin() included
            
            min_distance = float('inf')
            
            for customer in customers - agv.visited_customers:# Cycle through not visited customers
                    result = dijkstra(agv.current_node, customer)
                    if result is not None:
                        path, distance = result
                        min_distance = min(min_distance, distance)
                        if min_distance == distance:
                            min_path = path
                            min_customer = customer
            
            agv.current_target = min_customer # current_target is set to closest customer to depot
            agv.current_route = min_path
            
        if agv.current_node in set(['DP1', 'DP2']) and agv.visited_customers == customers and not agv.block:
            agv.current_target = 'START'
            route = dijkstra(agv.current_node, 'START')
            if route is not None:
                agv.current_route = route[0]
        
        
        if agv.current_node == 'START' and agv.current_target == 'START':
            agv.motorL.forward(50)
            agv.motorR.forward(50)
            sleep(2.4)
            agv.motorL.stop()
            agv.motorR.stop()
            break
            
            
if __name__ == "__main__":
    while True:
        if agv.button.value() == 1:
            main()
            break
    
'''
TODO: 
- Reduce sleep time at customers
'''

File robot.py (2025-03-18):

from machine import Pin
from time import sleep
import time
from sensors.tcs34725 import TCS34725
from pathfinder import dijkstra, convert_coord_to_node
from motors import Motor, Servo
from collections import deque


class Robot():
    
    def __init__(self, i2c_bus_1, pins, start, target1):
        
        
        # State Variables
        self.light = False # Boolean for light flashing
        self.current_node = start
        self.current_target = target1
        
        route = dijkstra(self.current_node, self.current_target)
        self.current_route = route[0] if route is not None else None  # List of nodes to visit
        
        self.current_direction = (0, 1) # starting direction as tuple
        self.next_direction = None
        

        self.block = False
        self.visited_customers = set()
        
        
        self.turning_prep_time = 0.55 # time required to move forward slightly before turning
        self._speed = 100
        
        #Line following params [PID control]
        
        self._window_size = 5
        self.left_sensor_hist = deque([0]*self._window_size, self._window_size)
        self.right_sensor_hist = deque([0]*self._window_size, self._window_size)
        self.left_outer_sensor_hist = deque([0]*self._window_size, self._window_size)
        self.right_outer_sensor_hist = deque([0]*self._window_size, self._window_size)
        self._prev_err = 0
        self._integral = 0
        self.kp = 40 # These are the correct values
        self.ki = 0.03
        self.kd = 3
        
        #I2C Sensors
        self.tcs = TCS34725(i2c_bus_1) # Colour Sensor
        
        #GPIO Connections
        self.button = Pin(pins['button_pin'], Pin.IN, Pin.PULL_DOWN)
        self.led = Pin(pins['led_pin'], Pin.OUT)
        self.line_sensorL = Pin(pins['line_sensorL_pin'], Pin.IN, Pin.PULL_DOWN) # Left Line Sensor
        self.line_sensorR = Pin(pins['line_sensorR_pin'], Pin.IN, Pin.PULL_DOWN) # Right Line Sensor
        self.outer_sensorL = Pin(pins['outer_sensorL_pin'], Pin.IN, Pin.PULL_DOWN) # Left Outer Sensor
        self.outer_sensorR = Pin(pins['outer_sensorR_pin'], Pin.IN, Pin.PULL_DOWN) # Right Outer Sensor
        
        #Motors and Servos
        self.motorR = Motor(4, 5) # Right Motor
        self.motorL = Motor(7, 6) # Left Motor
        self.servo1 = Servo(pins['servo_pin1']) # Servo 1
        self.servo2 = Servo(pins['servo_pin2']) # Servo 2

    def detect_junction(self):
        
        '''
        Detect junctions using outside line sensors\\
        Returns "junc" if a junction is detected, otherwise returns False\\
        '''

        outer_left_sensor = self.outer_sensorL.value()
        outer_right_sensor = self.outer_sensorR.value()
        
        self.left_outer_sensor_hist.append(outer_left_sensor)
        self.right_outer_sensor_hist.append(outer_right_sensor)

        outer_left_avg = self._get_moving_avg(self.left_outer_sensor_hist)
        outer_right_avg = self._get_moving_avg(self.right_outer_sensor_hist)

        if outer_left_avg > 0.8 or outer_right_avg > 0.8:
            return "junc"
        else:
            return False # No junction detected
    
    def forward(self, speed):
        '''
        Move the robot forward\\
        Continuously detects junctions and follows the line\\
        Stops the robot when the route is completed or an end condition is met\\
        No return value\\
        '''
        self._speed = speed
        
        while True:
            
            if self.visited_customers == set() and not self.block and self.current_node == '3':
                self.led.value(1)
            # FIXME: depending on whether we want more blocks we will need to change this condition also
            if self.visited_customers == set(['A', 'B', 'C', 'D']) and self.current_node == '3' and not self.block and self.current_target == 'START':
                self.led.value(0)
            
            
            junction = self.detect_junction()
            if junction == "junc":
                if self.current_route is not None:
    
                    '''
                     call decision
                     returns "left"[+], "right"[-] or "zero"
                     remove current node from route
                    '''
                    
                    decision = self.junction_decision()
                    
                    if decision is False: # end of route
                        self.current_node = convert_coord_to_node(self.current_route.pop(0)) # update current node
                        break
                    
                    self.turn(decision)
                    junction = False
                    
                    self.current_node = convert_coord_to_node(self.current_route.pop(0)) # update current node
                    
            self.follow_line()
        
        self.motorL.stop()
        self.motorR.stop()
       
    def _get_moving_avg(self, sensor_hist):
        '''
        Calculate the moving average of sensor readings\\
        Returns the moving average of the sensor readings\\
        '''
        return sum(sensor_hist)/len(sensor_hist)
    
    def follow_line(self):
        '''
        Follow the line using line sensors\\
        Uses PID control to adjust motor speeds based on sensor readings\\
        No return value\\
        '''
        left_sensor = self.line_sensorL.value()
        right_sensor = self.line_sensorR.value()
        
        self.left_sensor_hist.append(left_sensor)
        self.right_sensor_hist.append(right_sensor)
        
        left_avg = self._get_moving_avg(self.left_sensor_hist)
        right_avg = self._get_moving_avg(self.right_sensor_hist)
        
        err = right_avg - left_avg
        diff = err - self._prev_err
        self._integral += err
        self._prev_err = err
        
        correction = self.kp*err + self.ki*self._integral + self.kd*diff
        
        self.motorR.forward(100 - correction)
        self.motorL.forward(100 + correction)
       
    def turn(self, decision, with_prep = True):
        '''
        Turn the robot in the specified direction defined by the turn decision \\
        Parameters: \\
            decision: positive for left turn, negative for right turn, zero for straight \\
            with_prep: boolean indicating whether to move forward slightly before turning \\
        Updates the current direction after the turn \\
        No return value
        '''
        
        if decision > 0: # left turn
            
            # Moving average of the right sensor
            right_sensor_hist = deque([0]*10, 10)
            right_sensor_avg = self._get_moving_avg(right_sensor_hist)
            # moves forward slightly to allow room for turning
            if with_prep:
                self.motorR.forward(80)
                self.motorL.forward(80)
                sleep(self.turning_prep_time) # consider changing to a function of speed
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

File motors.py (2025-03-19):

from machine import Pin, PWM
from utime import sleep

class Motor():
    def __init__(self, dir_pin, pwm_pin):
        self.pwm = PWM(Pin(pwm_pin)) # set speed
        self.dir = Pin(dir_pin, Pin.OUT) # set direction
        self.dir.value(0) # set direction to forward
        self.pwm.freq(1000) # set max frequency
        self.pwm.duty_u16(0) # set duty cycle
        self.speed = 0
        self.rspeed = 0

    def forward(self, speed):
        if speed == self.speed:
            self.dir.value(0)
        else:
            self.speed = speed
            self.dir.value(0)
            self.pwm.duty_u16(int(65535*speed/100))

    def reverse(self, speed):
        if speed == self.rspeed:
            self.dir.value(1)
        else:
            self.rspeed = speed
            self.dir.value(1)
            self.pwm.duty_u16(int(65535*speed/100))

    def stop(self):
        self.pwm.duty_u16(0)

class Servo():
    def __init__(self, pwm_pin):
        self.pwm = PWM(Pin(pwm_pin)) # set speed
        self.pwm.freq(50) # set max frequency
        self.pwm.duty_u16(0) # set duty cycle

    def set_angle(self, angle):
        self.pwm.duty_u16(int(1802 - 7864 * angle / 270))

    def zero(self):
        self.pwm.duty_u16(0)
        

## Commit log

2025-02-22 refactoring - moved robot class to its own file and added motors.py for actuators and motors
2025-02-25 updated main.py, motors.py, robot.py
2025-02-25 junction detection and line following (PID VALUES NEED TO BE TUNED)
2025-02-26 Working motor code
2025-02-26 Updated pins on motors
2025-02-26 pin dict
2025-02-28 added CircuitBoardWiring Diagram
2025-02-28 added update to current state once turn is complete
2025-03-03 Added Route completion to junction_decision(). When route length is 0 or None, stop motors.
2025-03-04 updates current node state after turn decision is made
2025-03-04 fixed dijkstra indexing and added distance as output
    [pathfinder.py, robot.py]
2025-03-05 added i2c 2 to compmain.py
2025-03-06 fixing indexing and current_node updates
    [main.py, pathfinder.py, robot.py]
2025-03-13 fixed reverse from in drop
    [main.py, motors.py, robot.py]
2025-03-17 adjusted light pin
2025-03-18 fixed visited customers in 8 block sequence
    [main.py, round2Main.py]
2025-03-19 reduce motor inputs
2025-03-19 add rspeed for reverse to motors class
    [motors.py]
2025-03-22 added mech docs
    [Base.DXF, Battery Box 1.DXF, Battery Box 2.DXF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]
2025-03-24 updated mech docs
    [Base.DXF, Battery Box 1.DXF, Battery Box 2.DXF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]
